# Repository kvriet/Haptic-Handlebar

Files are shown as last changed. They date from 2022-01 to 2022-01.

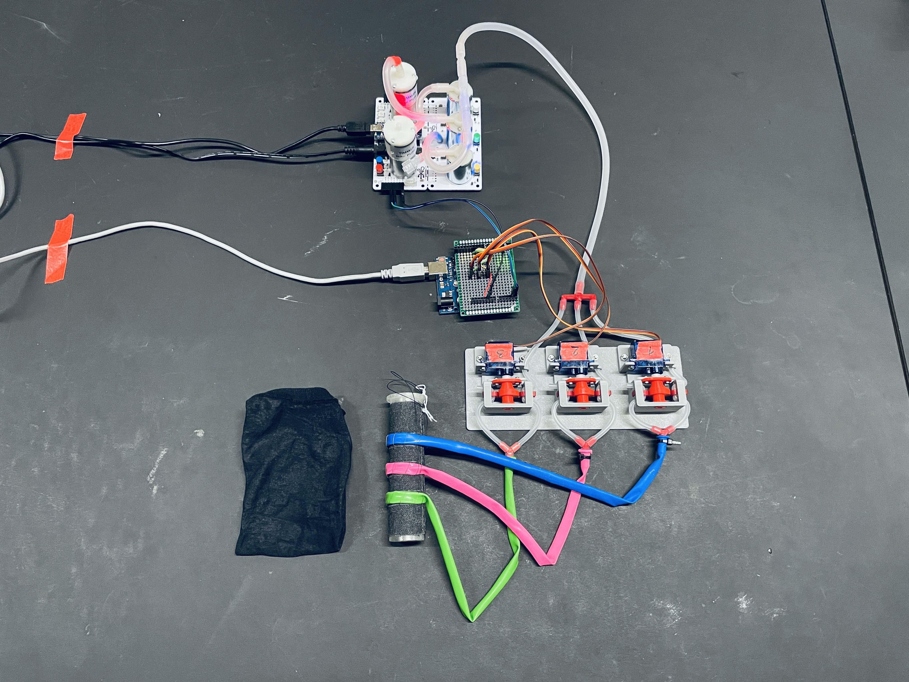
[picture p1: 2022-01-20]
full overview.JPG

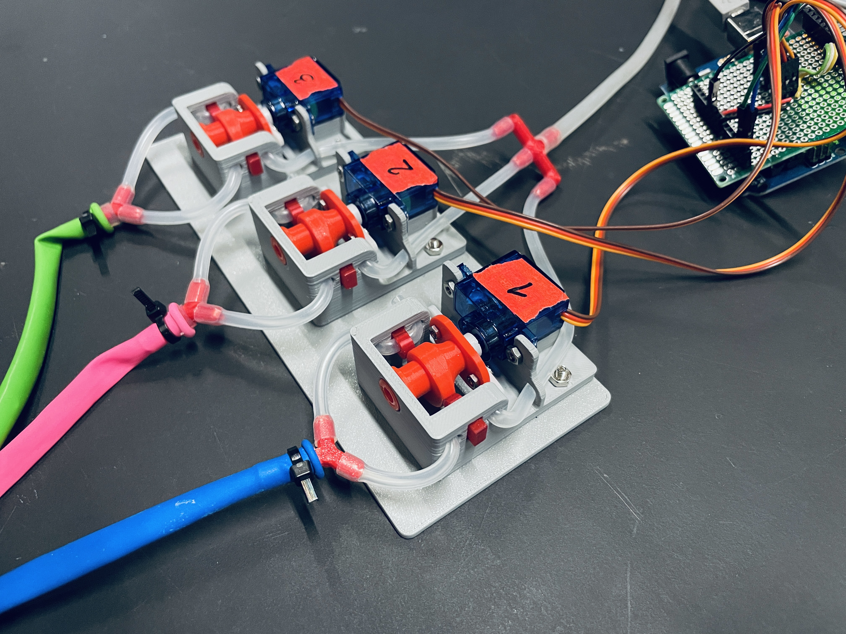
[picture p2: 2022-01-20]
servo rack overview.JPG

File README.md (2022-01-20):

Haptic Handlebar

Haptic Handlebar working

Bill of materials:
- Programmable Air (or air pump and pressure sensor): https://www.programmableair.com/
- Arduino Uno
- 3 mini servos: SG92R
- wires (flatcable)
- printing filament (PLA is sufficient)
- M2.5 and M3 nuts and bolts
- silicone tubing: 2mm ID 4mm OD; 4mm ID 6mm OD
- some party animal balloons (6mm diameter)
- fabric to sew the balloons to

Printing guide:
- tubing connectors should be printed at 0.1mm layer height, high quality
- other prints can be printed at 0.2mm layer height
- servo valves are inspired by mikey77's valves: https://www.instructables.com/3D-Print-Make-Servo-Controlled-Valves/

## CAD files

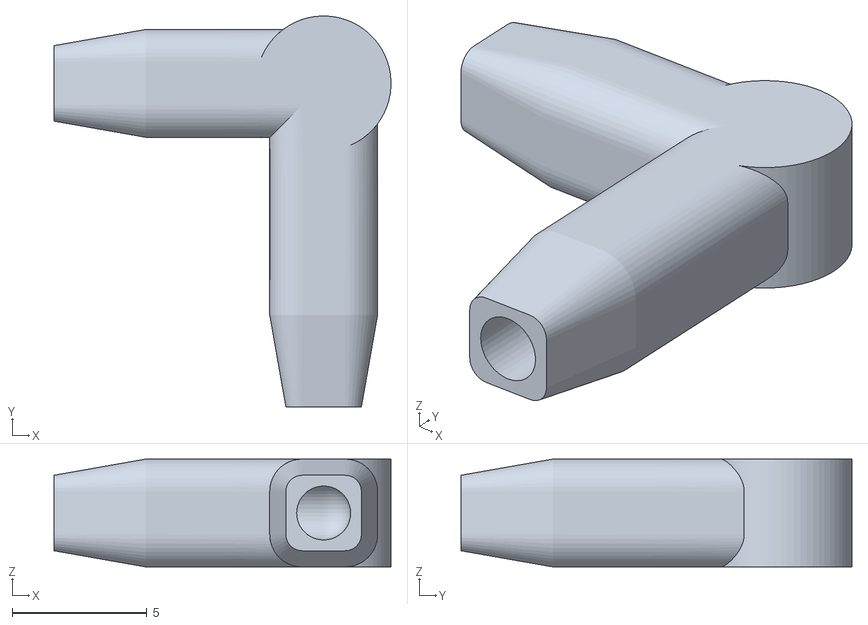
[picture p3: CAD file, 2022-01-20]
Printing Files/corner connector 2mm ID v1.stl
12.5 x 14.5 x 4.00

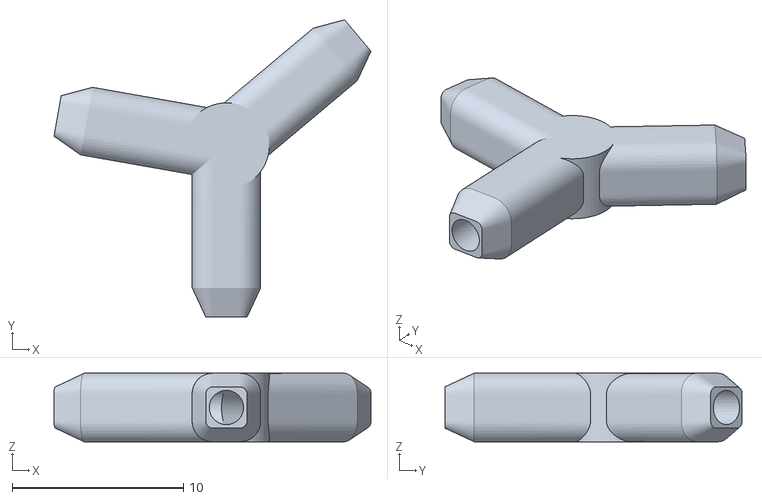
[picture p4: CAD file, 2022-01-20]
Printing Files/Y connector v2.stl
18.5 x 17.3 x 4.00

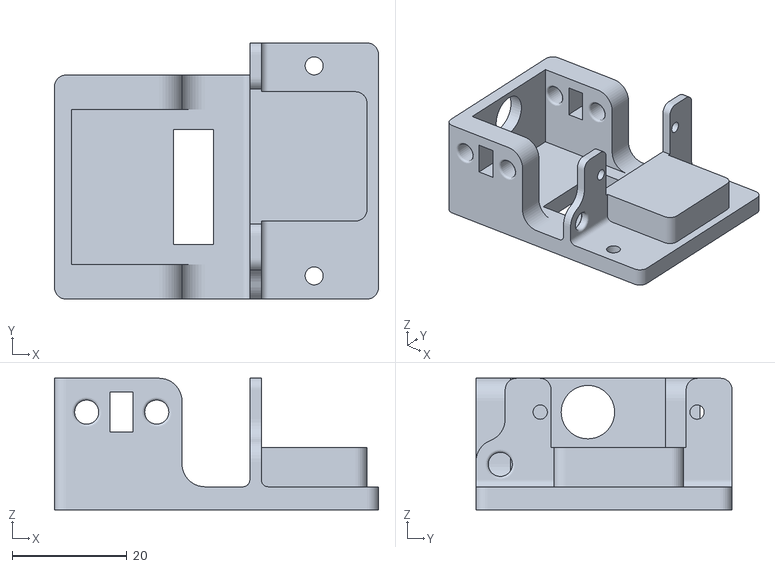
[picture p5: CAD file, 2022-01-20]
Printing Files/CAM frame single hole.stl
56.4 x 44.6 x 22.9

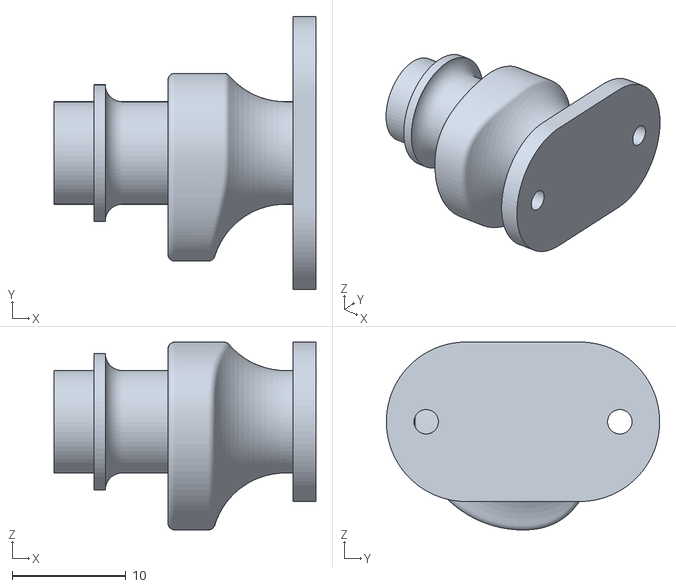
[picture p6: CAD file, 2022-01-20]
Printing Files/CAM 20mm half.stl
23.0 x 24.0 x 16.5

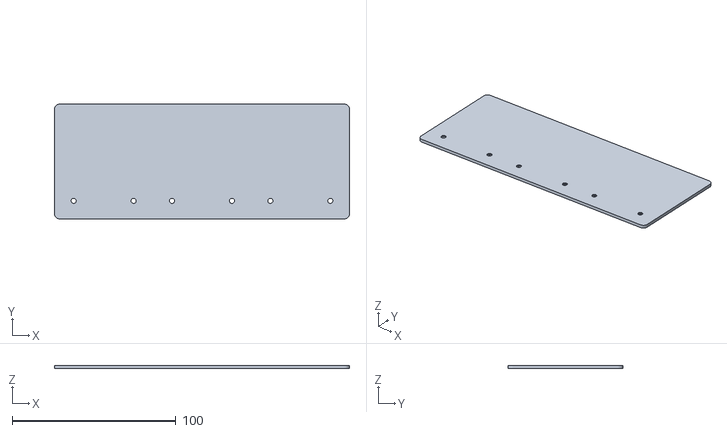
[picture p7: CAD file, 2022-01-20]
Printing Files/servo box bottom v2.stl
180.0 x 70.0 x 2.00

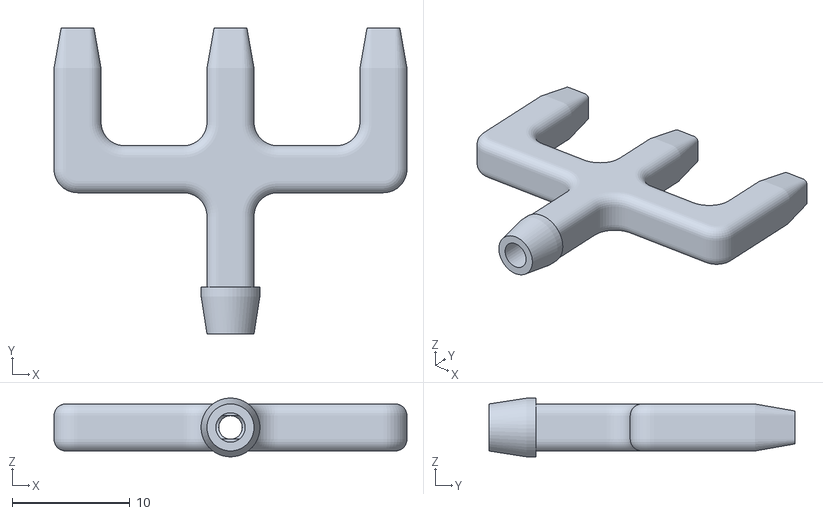
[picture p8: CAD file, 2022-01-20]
Printing Files/trident.stl
30.0 x 26.0 x 4.99

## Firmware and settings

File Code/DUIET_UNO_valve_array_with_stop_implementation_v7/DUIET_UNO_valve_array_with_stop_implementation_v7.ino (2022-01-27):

/* Code by Katrien van Riet - Jan 2022 */

#include <Servo.h>
#include <Wire.h>

// VARIABLES TO BE CHANGED //
int cols = 3; // Number of balloons
int rows = 12; // Number of values per balloon
int initialIntervalTime = 250;
int intervalDecrease = 50;
int timeIntervalInMilliseconds = initialIntervalTime;
int loopRepeat = 3;

int values[8][3][12] = {
  {{0, 0, 0, 0, 1, 1, 0, 0, 0, 0, 1, 1,}, {0, 0, 1, 1, 0, 0, 0, 0, 1, 1, 0, 0,}, {1, 1, 0, 0, 0, 0, 1, 1, 0, 0, 0, 0,}}
  ,
  {{1, 1, 0, 0, 0, 0, 1, 1, 0, 0, 0, 0,}, {0, 0, 1, 1, 0, 0, 0, 0, 1, 1, 0, 0,}, {0, 0, 0, 0, 1, 1, 0, 0, 0, 0, 1, 1,}}
  ,
  {{1, 1, 0, 0, 1, 1, 0, 0, 1, 1, 0, 0,}, {1, 1, 0, 0, 1, 1, 0, 0, 1, 1, 0, 0,}, {1, 1, 0, 0, 1, 1, 0, 0, 1, 1, 0, 0,}}
  ,
  {{1, 1, 0, 0, 1, 1, 0, 0, 1, 1, 0, 0,}, {0, 0, 0, 0, 0, 0, 0, 0, 0, 0, 0, 0,}, {0, 0, 0, 0, 0, 0, 0, 0, 0, 0, 0, 0,}}
  ,
  {{0, 0, 0, 0, 0, 0, 0, 0, 0, 0, 0, 0,}, {1, 1, 0, 0, 1, 1, 0, 0, 1, 1, 0, 0,}, {0, 0, 0, 0, 0, 0, 0, 0, 0, 0, 0, 0,}}
  ,
  {{0, 0, 0, 0, 0, 0, 0, 0, 0, 0, 0, 0,}, {0, 0, 0, 0, 0, 0, 0, 0, 0, 0, 0, 0,}, {1, 1, 0, 0, 1, 1, 0, 0, 1, 1, 0, 0,}}
  ,
  {{1, 1, 0, 0, 1, 1, 0, 0, 1, 1, 0, 0,}, {1, 1, 0, 0, 0, 0, 0, 0, 0, 0, 0, 0,}, {1, 1, 0, 0, 0, 0, 0, 0, 0, 0, 0, 0,}}
  ,
  {{1, 1, 0, 0, 1, 1, 0, 0, 1, 1, 0, 0,}, {0, 0, 1, 1, 0, 0, 1, 1, 0, 0, 1, 1,}, {1, 1, 0, 0, 1, 1, 0, 0, 1, 1, 0, 0,}}
};

// VARIABLES TO LEAVE ALONE //
long currentTime;
long prevTime;
int index = 0;
int angleOpen = 0;
int angleClosed = 90;
int loopIncrementer = 0;
int wireValue;
boolean isStopped = true;
boolean isLoopFinished = false;

Servo servos[3];

void setup() {
  servos[0].attach(9);
  servos[1].attach(10);
  servos[2].attach(11);
  Serial.begin(9600);
  Wire.begin(9);
  Wire.onReceive(receiveEvent);
}

void loop() {
  if (!isStopped) {
    if (!isLoopFinished) {
      currentTime = millis();
      if (currentTime - prevTime > timeIntervalInMilliseconds) {
        // Per time interval, loop through valves
        for (int i = 0; i < cols; i++) {
          if (values[wireValue - 1][i][index] == 0) {
            servos[i].write(angleClosed);
          } else if (values[wireValue - 1][i][index] == 1) {
            servos[i].write(angleOpen);
          }
          delay(5); // For stability
        }
        prevTime = currentTime;
        index++;
        if (index >= rows) {
          // If program is at end of row, loop back to front
          index = 0;
          loopIncrementer++;
          timeIntervalInMilliseconds -= intervalDecrease; // Every time the loop repeats, it is 25ms quicker per interval
        }
      }

      if (loopIncrementer >= loopRepeat) {
        loopIncrementer = 0;
        timeIntervalInMilliseconds = initialIntervalTime;
        isLoopFinished = true;
        closeAllServos();
      }
    }
  }
}

void closeAllServos() {
  for (int i = 0; i <= cols; i++) {
    servos[i].write(angleClosed);
    Serial.println("Close all servos");
  }
}

void receiveEvent(int bytes) {
  wireValue = Wire.read();    // read one character from the I2C
  isLoopFinished = false;
  if (wireValue == 0) {
    isStopped = true;
    closeAllServos();
    index = 0;
  }
  else {
    isStopped = false;
  }
}

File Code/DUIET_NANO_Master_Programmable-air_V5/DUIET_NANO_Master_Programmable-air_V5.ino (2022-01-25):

/*
  Code by Rory Aartsen - Jan 2022
*/

// Programmable-Air
// Author: tinkrmind
// https://github.com/orgs/Programmable-Air
//
// Factory Image
//
// PCB v1.0
#include <Wire.h>
#include "Timers.h"
#define BOARD_VER 6
#include "programmable_air.h"
#include <Adafruit_NeoPixel.h>
#include "EEPROMAnything.h"
Adafruit_NeoPixel paPixels(3, 12, NEO_GRB + NEO_KHZ800);

#define DEBUG 1

int state = UN_KNOWN;
int prevInput = 0;
boolean isLoopFinished = true;

#define MOTORS_ON 6
#define MOTORS_OFF 7

int calibratedPressure = 0;

void setup() {
  initializePins();
  pinMode(LED_BUILTIN, OUTPUT);
  pixels.begin();
  pixels.show();
  paPixels.begin();
  paPixels.show();
  Wire.begin();
  Serial.begin(9600);

}

void loop() {
  int pressure = readPressure();
  //delayWhileReadingPressure(200);
  int currentInput = serialEvent();

  if (currentInput != 0 && !isLoopFinished) {
    // If currrentInput != 0, the loop should run once (0 means stop)
    // And the loop is not finished yet, the code can run

    doBalloons();
    unsigned long currentMillis = millis();
    if (currentMillis - previousMillis >= interval) {

      isLoopFinished = true;
    }
  }
  // if pumping is done and no button is pressed, vent
  else if (isLoopFinished = true) {
    switchOffPumps();
    vent();
    state = VENTING;
  }
  Serial.println(pressure);
}

void doBalloons() {
  //if statement to make sure balloon doesn't blow up too much, but still blow up quickly
  if (readPressure() < 570) {
    // switch on pumps to 100% power
    switchOnPump(2, 100); // This last number is pump force 0-100%
    switchOffPump(1);
    blow();
    state = BLOWING;
    Serial.println("pressure lower than 550");
    readPressure();
  }

  else if (readPressure() > 569 && state == BLOWING) {
    // switch on pumps to 30% power
    switchOnPump(2, 35); // This last number is pump force 0-100%
    switchOffPump(1);
    blow();
    state = BLOWING;
    Serial.println("pressure higher than 550");
    readPressure();
  }
}


void error() {
  Serial.println("ERROR");
  for (int i = 0; i < 3; i++) {
    paPixels.setPixelColor(i, paPixels.Color(100, 0, 0));
  }
  paPixels.show();
  switchOffPumps();
  closeAllValves();
  while (1);
}

//void servoControl() {
//  unsigned long currentMillis = millis();
//
//  if (currentMillis - previousMillis >= interval) {
//    // save the last time you blinked the LED
//    previousMillis = currentMillis;
//    //    x = !x;
//    Serial.print("x = ");
//    Serial.println(x);
//
//    Wire.beginTransmission(9); // transmit to device #9
//    Wire.write(x);              // sends x
//    Wire.endTransmission();    // stop transmitting
//  }
//}

float serialEvent() {
  int input = Serial.read();
  if (input > 0) {
    isLoopFinished = false;
    previousMillis = millis();
  }
  switch (input) {
    case 0:
      Wire.beginTransmission(9); // transmit to device #9
      Wire.write(input);              // sends input
      Wire.endTransmission();    // stop transmitting
      isLoopFinished = true;
      break;
    case 1:
      digitalWrite(LED_BUILTIN, HIGH);
      Wire.beginTransmission(9); // transmit to device #9
      Wire.write(input);              // sends input
      Wire.endTransmission();    // stop transmitting
      break;
    case 2:
      digitalWrite(LED_BUILTIN, LOW);
      Wire.beginTransmission(9); // transmit to device #9
      Wire.write(input);              // sends input
      Wire.endTransmission();    // stop transmitting
      break;
    case 3:
      Wire.beginTransmission(9); // transmit to device #9
      Wire.write(input);              // sends input
      Wire.endTransmission();    // stop transmitting
      break;
    case 4:
      Wire.beginTransmission(9); // transmit to device #9
      Wire.write(input);              // sends input
      Wire.endTransmission();    // stop transmitting
      break;
    case 5:
      Wire.beginTransmission(9); // transmit to device #9
      Wire.write(input);              // sends input
      Wire.endTransmission();    // stop transmitting
      break;
    case 6:
      Wire.beginTransmission(9); // transmit to device #9
      Wire.write(input);              // sends input
      Wire.endTransmission();    // stop transmitting
      break;
    case 7:
      Wire.beginTransmission(9); // transmit to device #9
      Wire.write(input);              // sends input
      Wire.endTransmission();    // stop transmitting
      isLoopFinished = false;
      break;
    case 8:
      Wire.beginTransmission(9); // transmit to device #9
      Wire.write(input);              // sends input
      Wire.endTransmission();    // stop transmitting
      break;
    case 9:
      Wire.beginTransmission(9); // transmit to device #9
      Wire.write(input);              // sends input
      Wire.endTransmission();    // stop transmitting
      break;
    case 10:
      Wire.beginTransmission(10); // transmit to device #9
      Wire.write(input);              // sends input
      Wire.endTransmission();    // stop transmitting
      break;
  }
  return input;
}

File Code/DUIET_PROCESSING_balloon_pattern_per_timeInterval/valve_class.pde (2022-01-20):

class Valve {
  boolean isOpen = false;
  float posX, posY;
  int number;

  Valve (float x_, float y_, int n_) {
    posX = x_; 
    posY = y_;
    number = n_;
  }

  void run() { 
    // Check whether to move to next time increment
    if (values[number][index] == 0) {
      // Check whether servo should be open/closed
      isOpen = false;
    } else {
      isOpen = true;
    }
    //println(index);

    switch(number) {
    case 0:
      fill(0, 255, 0);
      break;
    case 1:
      fill(0, 50, 255);
      break;
    case 2:
      fill(255, 50, 150);
      break;
    }

    if (isOpen) {    
      arc(posX, posY, 60, 60, PI, TWO_PI);
    } else if (!isOpen) {
      arc(posX, posY, 30, 30, PI, TWO_PI);
    }
  }
}

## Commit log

2022-01-20 Uploaded all project files
    [CAM 20mm half.stl, Y connector v2.stl, corner connector 2mm ID v1.stl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]
2022-01-20 Auto stash before rebase of "origin/main"
    [Balloon visualisation V2.xlsx]
2022-07-26 added CAM frame single hole
    [CAM frame single hole.stl]
